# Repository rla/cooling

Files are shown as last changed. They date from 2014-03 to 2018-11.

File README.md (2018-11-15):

# avrcooling

PC cooling controller for rotary cooling devices (fans/pumps). It has
the following features:

 * Supports 4 cooling devices.
 * Can disable devices that still run on minimal PWM.
 * Monitors devices RPM.
 * RPM measurement supports pulse stretching.
 * Supports 2 thermal sensors.
 * Error signal output.
 * Can be controlled/queried over RS-232 interface.
 * Command-line client to query/debug/control the device.
 * Hardware design and source code is MIT-licensed.

### Control algorithm

The control algorithm uses 2 [decision tables](http://en.wikipedia.org/wiki/Decision_table),
one per thermal sensor. Table rows contain the following information:

 * enabled - whether the control row is enable.
 * min_temp - lower bound for activating the control row.
 * max_temp - upper bound for activating the control row.
 * affect_fan0 - whether to apply the row to fan 0.
 * affect_fan1 - whether to apply the row to fan 1.
 * affect_fan2 - whether to apply the row to fan 2.
 * affect_fan3 - whether to apply the row to fan 3.
 * fan0_pwm - PWM value to apply for fan 0.
 * fan1_pwm - PWM value to apply for fan 1.
 * fan2_pwm - PWM value to apply for fan 2.
 * fan3_pwm - PWM value to apply for fan 3.

There are 5 rows in each table. The first row with
min_temp...max_temp range including the current temperature is used for
applying the control values.

All cooling fans start initially in disabled state and with
0 PWM. When a fan PWM is set to a value greater than 0 then the fan power is
enabled. When PWM is set to 0 then the fan is also powered down.

Control table rows are checked periodically. The rows can be
read and updated using the command-line PC app described below.

## Project structure

The project is divided into 3 subdirectories:

 * `avr` - source for microcontroller binary.
 * `hw` - physical hardware design.
 * `pc` - NodeJS command-line app for communication.

## Hardware

### Pin allocation

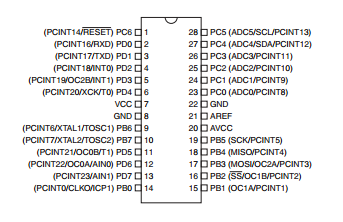
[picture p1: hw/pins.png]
Atmega88 pinout


 * pin  1: reset, connected to VCC and protected by zener diode
 * pin  2: USART RX line (pullup?)
 * pin  3: USART TX line
 * pin  4: PD2, Error signal output
 * pin  5: PD3, OC2B, fan 4 PWM output
 * pin  6: PD4, not connected
 * pin  7: VCC
 * pin  8: GND
 * pin  9: XTAL 1
 * pin 10: XTAL 2
 * pin 11: PD5, OC0B, fan 2 PWM output
 * pin 12: PD6, OC0A, fan 1 PWM output
 * pin 13: PD7, not connected
 * pin 14: PB0, fan 1 enable
 * pin 15: PB1, fan 2 enable
 * pin 16: PB2, fan 3 enable
 * pin 17: PB3, fan 3 PWM output
 * pin 18: PB4, fan 4 enable
 * pin 19: PB5, not connected
 * pin 20: AVCC, connected to VCC through low-pass filter L1/C13
 * pin 21: AREF, analog reference, decoupled with 100nF cap C10
 * pin 22: GND
 * pin 23: PC0, ADC0, temperature sensor 1 input, low-pass filter R5/C7
 * pin 24: PC1, ADC1, temperature sensor 2 input, low-pass filter R3/C8
 * pin 25: PC2, fan 1 RPM input, pull-up, low-pass filter R10/C9
 * pin 26: PC3, fan 2 RPM input, pull-up, low-pass filter R9/C11
 * pin 27: PC4, fan 3 RPM input, pull-up, low-pass filter R8/C12
 * pin 28: PC5, fan 4 RPM input, pull-up, low-pass filter R7/C14

### Port directions

#### Port B

 * PB0 - output (fan 1 enable)
 * PB1 - output (fan 2 enable)
 * PB2 - output (fan 3 enable)
 * PB3 - output (fan 3 PWM)
 * PB4 - output (fan 4 enable)
 * PB5 - output (not connected)
 * PB6 - output (overriden by xtal)
 * PB7 - output (overriden by xtal)

#### Port C

 * PC0 - input (ADC)
 * PC1 - input (ADC)
 * PC2 - input (fan 1 RPM, pull-up)
 * PC3 - input (fan 2 RPM, pull-up)
 * PC4 - input (fan 3 RPM, pull-up)
 * PC5 - input (fan 4 RPM, pull-up)
 * PC6 - input (default reset config)
 * PC7 - not in circuit/registry

#### Port D

 * PD0 - output (overriden by USART)
 * PD1 - output (overriden by USART)
 * PD2 - output (error)
 * PD3 - output (fan 4 PWM)
 * PD4 - output (not connected)
 * PD5 - output (fan 2 PWM)
 * PD6 - output (fan 1 PWM)
 * PD7 - output (not connected)

### Full schematics

Full schematics in Eagle format can be found in the file `hw/schematics.sch`.

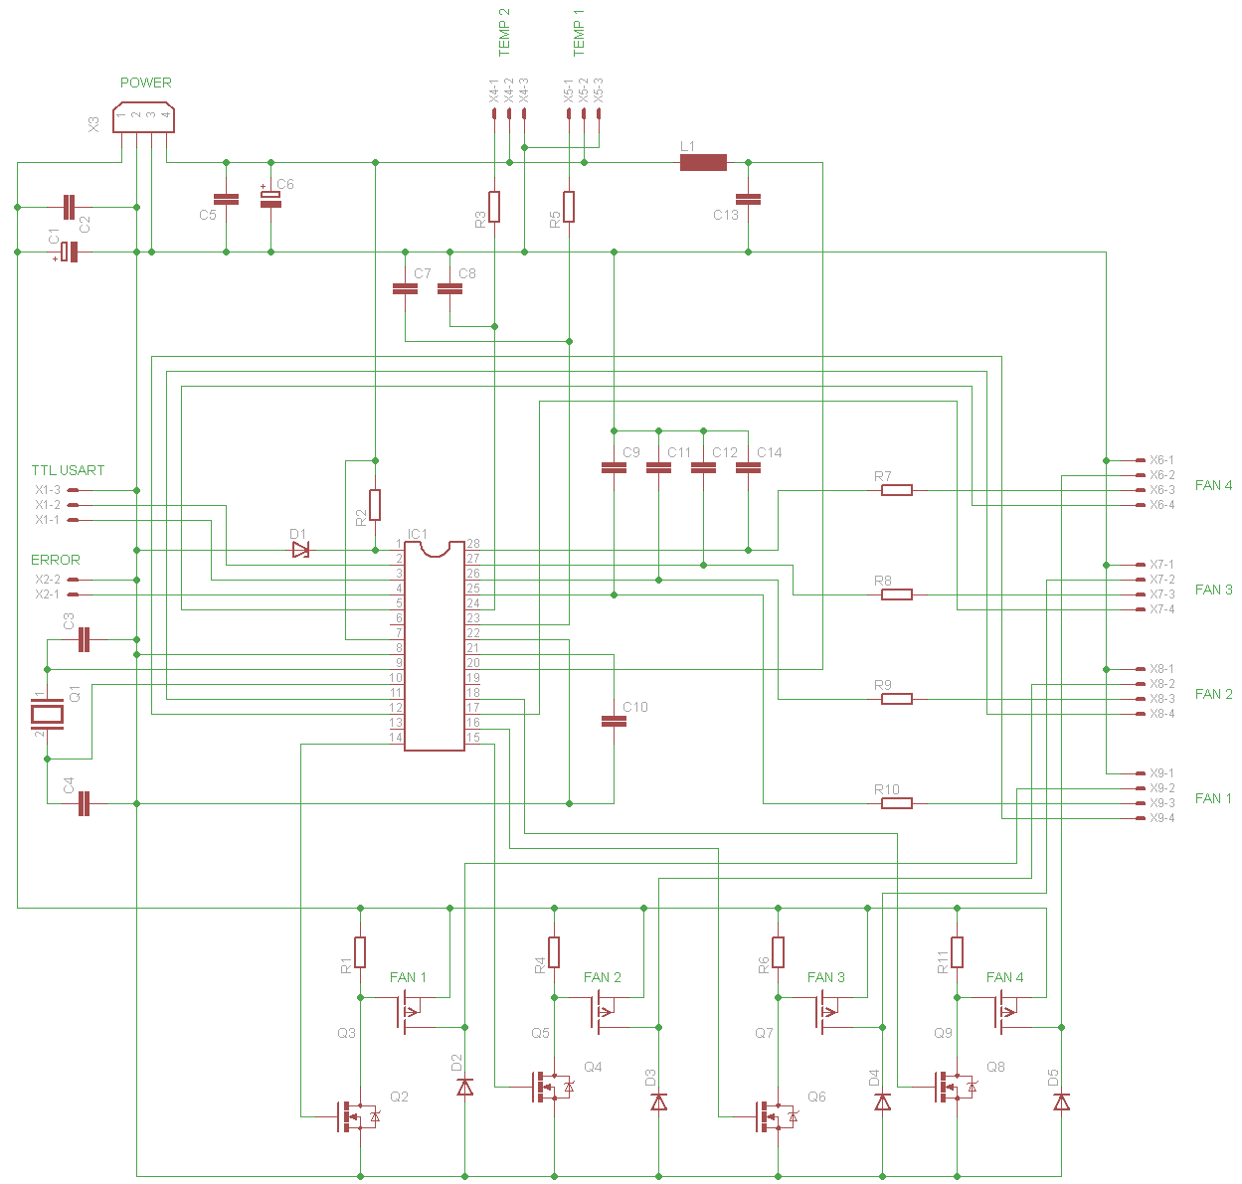
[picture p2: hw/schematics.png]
Full schematics


#### Part list

 * C1 10uF/16V
 * C2 100nF/63V 5mm
 * C3, C4 22pF/63V 2.54mm
 * C5 100nF/63V 5mm
 * C6 10uF/16V 5mm
 * C7, C8 10nF/100V 5mm
 * C9, C11, C12, C14 10nF/63V 5mm
 * C10 100nF/63V 5mm
 * C13 100nF/63V 5mm
 * D1 5.1V zener 7.62mm
 * D2, D3, D4, D5 2N4007
 * IC1 Atmega88 DIP28
 * R1, R2, R3, R4, R5, R6, R7, R8, R9, R10, R11 10k
 * Q1 12MHz
 * Q2, Q4, Q6, Q8 2N7000
 * Q3, Q5, Q7, Q9 IRF9530
 * L1 10uH
 * X3 molex power connector, [Farnell product page](http://uk.farnell.com/jsp/search/productdetail.jsp?SKU=1391827)
 * X6, X7, X8, X9 molex 47053-1000 headers, [Farnell product page](http://uk.farnell.com/jsp/search/productdetail.jsp?SKU=2313705)

### Board layout

Board layout in Eagle format can be found in the file `hw/board.brd`. Layout
suitable for tone-transfer can be found in the PDF file `hw/board.pdf`.

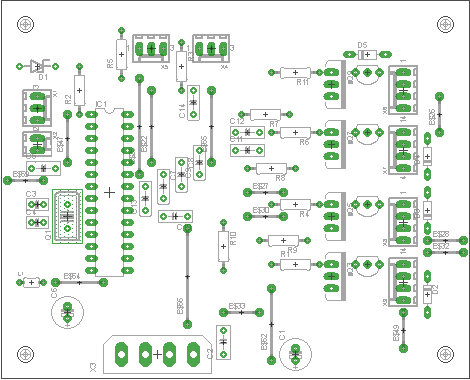
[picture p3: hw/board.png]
Board layout


Photo of 2 completed units:

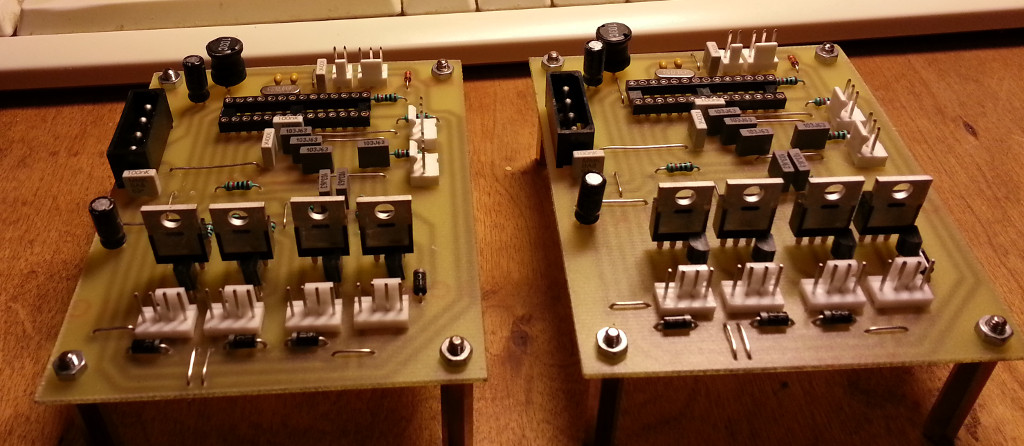
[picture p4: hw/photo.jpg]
2 completed units


### Fan connectors

4-wire connectors are standardized in the [specification](http://www.formfactors.org/developer%5Cspecs%5C4_Wire_PWM_Spec.pdf).
Connector pinout with typical wire colors is:

 * 1 - GND - black
 * 2 - 12V - yellow
 * 3 - RPM - green
 * 4 - PWM - blue

The max fan current is limited by switch MOSFET channel resistance in ON mode.
This is about 0.3 Ohms. Max dissipation of 1W gives the max current of about 1.9A.

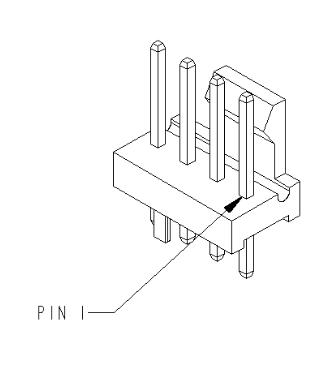
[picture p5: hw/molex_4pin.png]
4-pin molex


#### 3-wire connectors

3-wire connectors lack PWM signal but are otherwise compatible with
4-wire headers. Pinout:

 * 1 - GND - black
 * 2 - 12V - red
 * 3 - RPM - yellow

While a 3-wire fan lacks PWM control, it can still be made variable-speed by
modulating the supply voltage. This can be implemented with the following
circuit:

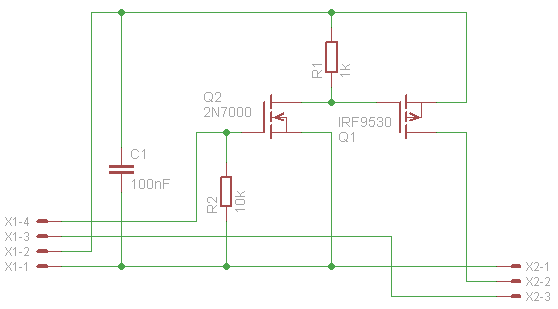
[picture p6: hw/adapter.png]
3-wire to 4-wire adapter


#### Temp. sensor connectors

These connect MCP9700 to the board. There can be up to 2 sensors
connected. The system assumes 0.5V offset and 10mv per °C. This can be
changed by recompiling the firmware.

 * 1 - sensor output
 * 2 - sensor power (5V)
 * 3 - GND

#### Error signal connector

Error signal is set high whenever an enabled fan's RPM
reads 0. The signal comes directly from MCU and cannot
be directly loaded with higher current than 40mA.

 * 1 - error signal
 * 2 - GND

#### RS-232 interface

The RS-232 interface is used for updating the control line tables and
for debugging the device. The connector is denoted as X1 on schematics
and board and has the following pinout:

 * 1 - TX line
 * 2 - RX line
 * 3 - GND

A level translator has to be used for connecting the device to PC. PC
uses signal levels -12V/+12V while the device uses normal TTL levels 0V/5V.

A level translator can be built using the [MAX232](http://www.ti.com/lit/ds/symlink/max232.pdf)
chip or using a prebuilt module/cable/converter. There are various circuits and
building instructions on the Internet.

### Compiling firmware

The project contains a Makefile that includes build targets
with [avr-gcc](http://www.nongnu.org/avr-libc/) compiler.

To build the HEX binary for the controller:

    cd avr
    make

If [avrdude](http://www.nongnu.org/avrdude/) is installed then the hex file
can be burned into the device with the command:

    make burn

### Fuses

 * Clock: Full-swing crystal, BOD enabled
 * BOD 4.3V

#### Low fuse

 * CKDIV8 1 (unprogrammed)
 * CKOUT 1 (unprogrammed)
 * SUT1 0 (crystal, BOD enabled)
 * SUT0 1 (crystal, BOD enabled)
 * CKSEL3 0
 * CKSEL2 1
 * CKSEL1 1
 * CKSEL0 1

CKSEL is for full-swing crystal osc. lfuse total 11010111 = 0xd7.

#### High fuse

 * RSTDISBL 1 (unprogrammed)
 * DWEN 1 (unprogrammed)
 * SPIEN 0 (programmed)
 * WDTON 1 (unprogrammed)
 * EESAVE 1 (unprogrammed)
 * BODLEVEL2 1
 * BODLEVEL1 0
 * BODLEVEL0 0

hfuse total 11011100 = 0xdc.

If avrdude is installed then correct fuses can be burned
using the command:

    make burn-fuse

## Client

The client application is used for updating the control table lines
and for debugging the device.

Client options and supported commands:

```
Usage: avrcooling --port <port> --command <command> [arguments]
Recognized commands:
  disable0       disable fan 0
  disable1       disable fan 1
  disable2       disable fan 2
  disable3       disable fan 3
  echo           sends and receives the given byte
  enable0        enable fan 0
  enable1        enable fan 1
  enable2        enable fan 2
  enable3        enable fan 3
  nostretch0     disable pulse stretch for fan 0
  nostretch1     disable pulse stretch for fan 1
  nostretch2     disable pulse stretch for fan 2
  nostretch3     disable pulse stretch for fan 3
  pwm0_get       query fan 0 PWM level (0-255)
  pwm0_set       set fan 0 PWM (0-255)
  pwm1_get       query fan 1 PWM level (0-255)
  pwm1_set       set fan 1 PWM (0-255)
  pwm2_get       query fan 2 PWM level (0-255)
  pwm2_set       set fan 2 PWM (0-255)
  pwm3_get       query fan 3 PWM level (0-255)
  pwm3_set       set fan 3 PWM (0-255)
  rpm0           query fan 0 RPM
  rpm1           query fan 1 RPM
  rpm2           query fan 2 RPM
  rpm3           query fan 3 RPM
  stretch0       enable pulse stretch for fan 0
  stretch1       enable pulse stretch for fan 1
  stretch2       enable pulse stretch for fan 2
  stretch3       enable pulse stretch for fan 3
  stretch_info   query pulse stretch settings
  temp0          query sensor 0 temperature
  temp0_line_get get control table line (0-4) for sensor 0
  temp0_line_set set control table line (0-4) for sensor 0
  temp1          query sensor 1 temperature
  temp1_line_get get control table line (0-4) for sensor 1
  temp1_line_set set control table line (0-4) for sensor 1

```

### Debugging

Set environment variable `DEBUG=*` and run the command.

    DEBUG=* avrcooling ...

### Installation

Assuming that you have [NodeJS](https://nodejs.org/) installed:

    npm install -g avrcooling

### Protocol

The client-device communication protocol terminates messages with line ends.
Data on individual lines is encoded in the hex encoding.

Decoded commands have the following format:

    [command_byte, arguments..., checksum_byte]

Responses have the following format:

    [response_ok, response arguments..., checksum_byte]

or

    [response_fail, checksum_byte]

or

    [command_checksum_fail, checksum_byte]

Multibyte integers are sent in big-endian format. Maximum decoded message length is 10 bytes.
The detailed description of the protocol is found in [pc/lib/commands.js](pc/lib/commands.js).

The checksum computation uses the Pearson hash algorithm:
<http://en.wikipedia.org/wiki/Pearson_hashing>. The constants
table can be found in [avr/src/pearson.c](avr/src/pearson.c).

## Changelog

 * 2018-11-11 Do not reset PWM on disable. Implement missing get-pwm command.
   Reset RPM only on timeout preventing sporadic 0 RPM responses. Update RPM
   atomically preventing potentially corrupted responses due to data race.
 * 2016-01-31 BOD (brown-out detection) enabled.
 * 2015-03-24 Pulse stretching is implemented. Client code is finished.
 * 2014-07-27 Client code is mostly working.
 * 2014-07-17 AVR code is mostly working.
 * 2014-02-01 Physical hardware design is ready.

## Known issues

 * Max ADC input voltage is 1.1V when the internal reference is selected (by default).
 * Temperature sensor MCP9700 needs 100nF decoupling cap at the sensor to ensure
   stable operation.

## License

The MIT License. See the LICENSE file.

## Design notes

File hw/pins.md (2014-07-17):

# Algorithm

## PWM generation

PWM signal is generated by timers.

## RPM measurement

RPM is measured by finding time between two RPM pulses using the 16-bit Timer1.
Pulses are detected using polling on input pins.

# Atmega88 pin allocation

Atmega88 pinout

 * pin  1: reset, connected to VCC and protected by zener diode
 * pin  2: USART RX line (pullup?)
 * pin  3: USART TX line
 * pin  4: PD2, Error signal output
 * pin  5: PD3, OC2B, fan 4 PWM output
 * pin  6: PD4, not connected
 * pin  7: VCC
 * pin  8: GND
 * pin  9: XTAL 1
 * pin 10: XTAL 2
 * pin 11: PD5, OC0B, fan 2 PWM output
 * pin 12: PD6, OC0A, fan 1 PWM output
 * pin 13: PD7, not connected
 * pin 14: PB0, fan 1 enable
 * pin 15: PB1, fan 2 enable
 * pin 16: PB2, fan 3 enable
 * pin 17: PB3, fan 3 PWM output
 * pin 18: PB4, fan 4 enable
 * pin 19: PB5, not connected
 * pin 20: AVCC, connected to VCC through low-pass filter L1/C13
 * pin 21: AREF, analog reference, decoupled with 100nF cap C10
 * pin 22: GND
 * pin 23: PC0, ADC0, temperature sensor 1 input, low-pass filter R5/C7
 * pin 24: PC1, ADC1, temperature sensor 2 input, low-pass filter R3/C8
 * pin 25: PC2, fan 1 RPM input, pull-up, low-pass filter R10/C9
 * pin 26: PC3, fan 2 RPM input, pull-up, low-pass filter R9/C11
 * pin 27: PC4, fan 3 RPM input, pull-up, low-pass filter R8/C12
 * pin 28: PC5, fan 4 RPM input, pull-up, low-pass filter R7/C14

## Port directions

Port B

 * PB0 - output (fan 1 enable)
 * PB1 - output (fan 2 enable)
 * PB2 - output (fan 3 enable)
 * PB3 - output (fan 3 PWM)
 * PB4 - output (fan 4 enable)
 * PB5 - output (not connected)
 * PB6 - output (overriden by xtal)
 * PB7 - output (overriden by xtal)

Port C

 * PC0 - input (ADC)
 * PC1 - input (ADC)
 * PC2 - input (fan 1 RPM, pull-up)
 * PC3 - input (fan 2 RPM, pull-up)
 * PC4 - input (fan 3 RPM, pull-up)
 * PC5 - input (fan 4 RPM, pull-up)
 * PC6 - input (default reset config)
 * PC7 - not in circuit/registry

Port D

 * PD0 - output (overriden by USART)
 * PD1 - output (overriden by USART)
 * PD2 - output (error)
 * PD3 - output (fan 4 PWM)
 * PD4 - output (not connected)
 * PD5 - output (fan 2 PWM)
 * PD6 - output (fan 1 PWM)
 * PD7 - output (not connected)

## Fuses

Clock selection: full swing crystal

 * CKSEL 0111
 * SUT 11 (slow raising power)
 * Low fuse result: 0xf7

## Registers

 * OSCCAL - Oscillator calibration register - NO CHANGE
 * CLKPR - Clock prescale register - NO CHANGE
 * SMCR - Sleep mode control register - NO CHANGE
 * PRR - Power reduction register - NO CHANGE
 * MCUSR - MCU status register - NO CHANGE
 * WDTCSR - Watchdog timer control register - NO CHANGE
 * MCUCR - MCU control register - interrupts through `sei()`
 * EICRA - External interrupt control register A - NO CHANGE
 * EIMSK - External interrupt mask register - NO CHANGE
 * EIFR - External interrupt flag register - NO CHANGE
 * PCICR - Pin change interrupt control register - NO CHANGE
 * PCIFR - Pin change interrupt flag register - NO CHANGE
 * PCMSK2 - Pin change mask register 2 - NO CHANGE
 * PCMSK1 - Pin change mask register 1 - NO CHANGE
 * PCMSK0 - Pin change mask register 0 - NO CHANGE
 * PINB - The port B input pins address - NOT USED
 * PIND - The port D input pins address - NOT USED
 * GTCCR - General timer/counter control register - NO CHANGE
 * SPCR – SPI control register - NO CHANGE
 * SPSR – SPI status register - NOT USED
 * SPDR – SPI data register - NOT USED

### Port B

 * DDRB - The port B data direction register. As port B is
   configured as output then all bit are set to 1.
 * PORTB - The port B data register. Used for controlling the fans.

### Port C

 * DDRC - The port C data direction register- As port C is used as
   input then no change is needed as it is configured as input by default.
 * PORTC - The port C data register. Some bits need to be written 1 to
   enable pull-ups.
 * PINC - The port C input pins address. Used for polling fans PWM.

### Port D

 * PORTD - The port D data register. Used for error signal. Other
   functions are overriden (USART, PWM).
 * DDRD - The port D data direction register. As port B is configured
   as output then all bit are set to 1.

### Timer 0

Timer 0 needs to be configured in phase-correct PWM mode.

 * TCCR0A - Timer/counter control register A.
 * TCCR0B - Timer/counter control register B.
 * TCNT0 - Timer/counter register.
 * OCR0A - Output compare register A.
 * OCR0B - Output compare register B.
 * TIMSK0 - Timer/counter interrupt mask register - NO CHANGE
 * TIFR0 - Timer/Counter0 interrupt flag register - NO CHANGE

### Timer 1

Timer 1 is used for counting time between RPM pulses and
detecting timeout.

 * TCCR1A – Timer/Counter1 control register A.
 * TCCR1B – Timer/Counter1 control register B.
 * TCCR1C – Timer/Counter1 control register C - NO CHANGE
 * TCNT1H and TCNT1L – Timer/Counter1.
 * OCR1AH and OCR1AL – Output compare register 1 A.
 * OCR1BH and OCR1BL – Output compare register 1 B.
 * ICR1H and ICR1L – Input capture register 1. NO CHANGE/NOT USED
 * TIMSK1 – Timer/Counter1 interrupt mask register
 * TIFR1 – Timer/Counter1 interrupt flag register

### Timer 2

Timer 2 needs to be configured in phase-correct PWM mode.

 * TCCR2A – Timer/counter control register A.
 * TCCR2B – Timer/counter control register B.
 * TCNT2 – Timer/counter register.
 * OCR2A – Output compare register A.
 * OCR2B – Output compare register B.
 * TIMSK2 – Timer/Counter2 interrupt mask register - NO CHANGE
 * TIFR2 – Timer/Counter2 interrupt flag register - NO CHANGE
 * ASSR – Asynchronous status register - NO CHANGE

### USART

TODO

### ADC

ADC reference is set to AVcc.

 * ADCSRB – ADC Control and Status Register B - NO CHANGE
 * ACSR – Analog Comparator Control and Status Register - NO CHANGE
 * DIDR1 – Digital Input Disable Register 1 - NO CHANGE
 * ADMUX – ADC Multiplexer Selection Register
 * ADCSRA – ADC Control and Status Register A
 * ADCL and ADCH – The ADC Data Register
 * ADCSRB – ADC Control and Status Register B
 * DIDR0 – Digital Input Disable Register 0

FIXME - use watchdog?
http://www.embedds.com/using-watchdog-timer-in-your-projects/

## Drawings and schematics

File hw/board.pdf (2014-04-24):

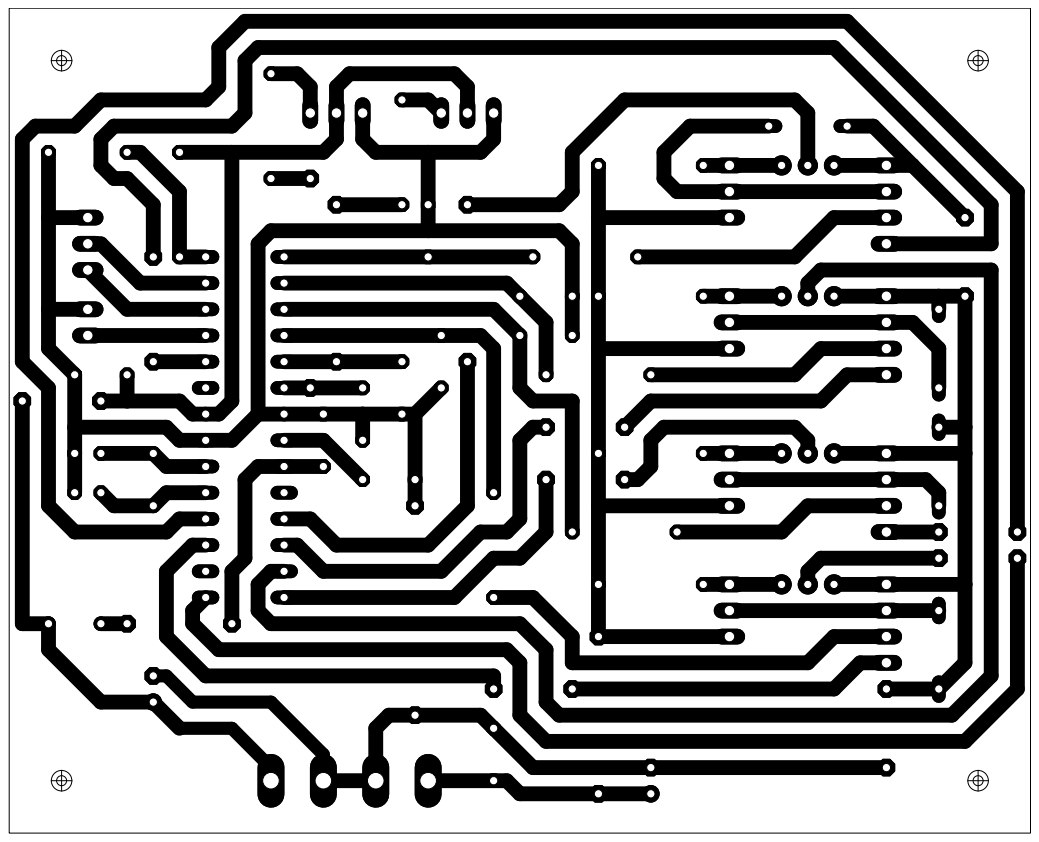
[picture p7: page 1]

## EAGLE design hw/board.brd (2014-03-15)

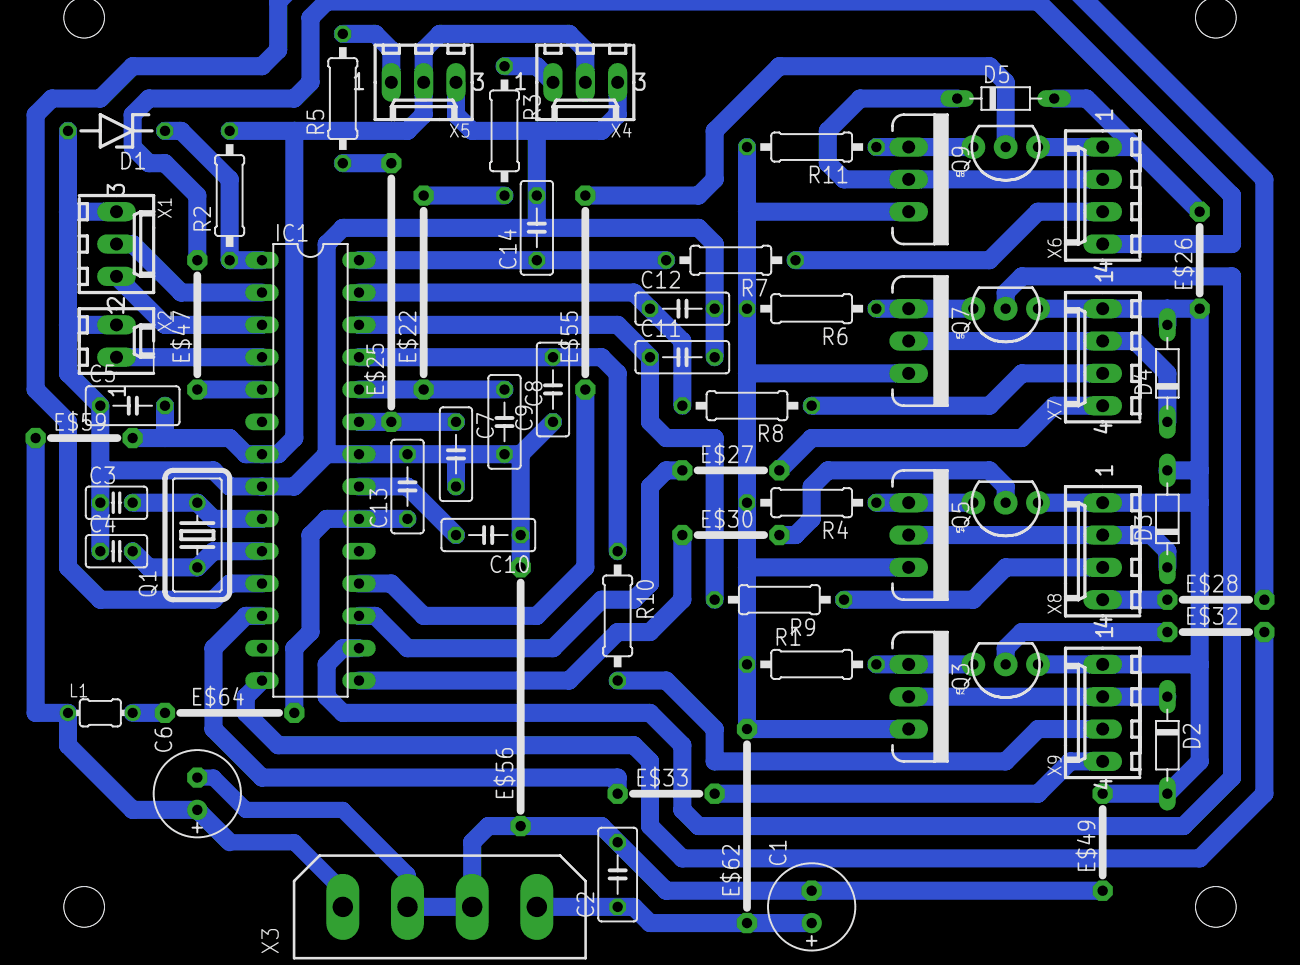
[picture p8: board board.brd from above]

Board: 2 copper layers, 65 parts (0 on the bottom side), 35 nets.

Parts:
C1, C6: E2,5-7
C2, C5: C050-030X075
C3, C4: C025-025X050
C7, C8, C9, C10, C11, C12, C13, C14: C050-025X075
D1: ZDIO-7.5
D2, D3, D4, D5: D-7.5
E$22, E$55, E$62: 15
E$25, E$56: 20
E$26, E$27, E$28, E$30, E$32, E$33, E$49, E$59: 07
E$47, E$64: 10
IC1: DIL28-3
L1: LAL02
Q1: HC18U-V
Q2, Q4, Q6, Q8: TO-92-AMMO
Q3, Q5, Q7, Q9: TO220V
R1, R2, R3, R4, R5, R6, R7, R8, R9, R10, R11: 0207/10
X1, X4, X5: 6410-03
X2: 6410-02
X3: 9090-4V
X6, X7, X8, X9: 6410-04

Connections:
S$1: D2.A, D3.A, D4.A, E$49.2, Q2.1, Q4.1, Q6.1, X7.1, X8.1, X9.1
S$2: D5.C, Q9.2, X6.2
S$3: D4.C, Q7.2, X7.2
S$4: D3.C, Q5.2, X8.2
S$5: D2.C, Q3.2, X9.2
S$6: E$62.2, Q3.3, Q5.3, Q7.3, Q9.3, R1.1, R4.2, R6.2, R11.2
S$8: Q2.3, Q3.1, R1.2
S$9: C11.1, R9.2
S$10: Q6.3, Q7.1, R6.1
S$11: Q8.3, Q9.1, R11.1
S$12: R7.1, X6.3
S$13: R8.1, X7.3
S$14: R9.1, X8.3
S$15: R10.2, X9.3
S$16: C12.1, R8.2
S$17: E$32.1, Q2.2
S$18: C9.2, R10.1
S$20: C5.2, E$59.2, R2.2, X4.2, X5.2
S$22: E$47.2, X6.4
S$24: E$55.2, Q8.2
S$30: E$28.1, X8.4
S$31: C3.1, C4.1, C7.2, C8.2, C9.1, C10.1, C11.2, C12.2, D1.A, E$56.2, X1.3, X2.2, X4.3, X5.3
S$33: D5.A, Q8.1, X6.1
S$34: C13.1, E$64.2
S$38: C3.2, Q1.2
S$39: D1.C, R2.1
S$40: C4.2, Q1.1
S$41: E$22.2, R3.2
S$42: C1.+, E$62.1, X3.4
S$43: R5.2, X5.1
S$45: E$59.1, L1.1, X3.1
S$46: Q4.3, Q5.1, R4.1
S$48: R3.1, X4.1
S$51: C6.-, E$49.1, E$56.1, X3.2, X3.3
S$57: E$64.1, L1.2

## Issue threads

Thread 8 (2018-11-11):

Missing ground in schematic

n3vu0r, 2018-11-11:
In contrast to the board files, the schematic is missing a connection to ground at the wire on the very bottom.

rla, 2018-11-11:
Thank you for pointing it out. I'm going to fix it and re-generate schematics png file too.

rla, 2018-11-19:
Fixed in https://github.com/rla/cooling/commit/cf06339031158de418d635c599184153563e54af

Closed 2018-11-19.

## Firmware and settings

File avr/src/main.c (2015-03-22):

#define F_CPU 12000000UL

#include <avr/io.h>
#include <avr/interrupt.h>
#include <util/delay.h>
#include <util/atomic.h>
#include <avr/eeprom.h>

#include "init.c"
#include "fans.c"
#include "init_fans.c"
#include "adc.c"
#include "measure.c"
#include "rpm.c"
#include "adjust.c"
#include "error.c"
#include "hex.c"
#include "usart_buffer.c"
#include "pearson.c"
#include "protocol.c"
#include "usart_run.c"

int main() {

    init();
    init_fans(0);

    uint8_t start_wait = 0;

    while (1) {

        if (!measure_timeout) {

            rpm_measure();

            if (!measure_timeout) {

                measure_timeout = 1;
            }

            // Wait some time before enabling
            // the adjustment algorithm.

            if (start_wait < 10) {

                start_wait += 1;

            } else {

                adjust();

                check_error();
            }
        }
    };

    return 1;
}

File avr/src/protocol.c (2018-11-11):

#define COMMAND_ADC_0 1
#define COMMAND_ADC_1 2

#define COMMAND_GET_RPM_0 3
#define COMMAND_GET_RPM_1 4
#define COMMAND_GET_RPM_2 5
#define COMMAND_GET_RPM_3 6

#define COMMAND_SET_PWM_0 7
#define COMMAND_SET_PWM_1 8
#define COMMAND_SET_PWM_2 9
#define COMMAND_SET_PWM_3 10

#define COMMAND_GET_PWM_0 11
#define COMMAND_GET_PWM_1 12
#define COMMAND_GET_PWM_2 13
#define COMMAND_GET_PWM_3 14

#define COMMAND_ENABLE_0 15
#define COMMAND_ENABLE_1 16
#define COMMAND_ENABLE_2 17
#define COMMAND_ENABLE_3 18

#define COMMAND_DISABLE_0 19
#define COMMAND_DISABLE_1 20
#define COMMAND_DISABLE_2 21
#define COMMAND_DISABLE_3 22

#define COMMAND_TEMP0_SET 23
#define COMMAND_TEMP1_SET 24

#define COMMAND_TEMP0_GET 25
#define COMMAND_TEMP1_GET 26

#define COMMAND_GET_STRETCH 27

#define COMMAND_STRETCH_ENABLE_0 28
#define COMMAND_STRETCH_ENABLE_1 29
#define COMMAND_STRETCH_ENABLE_2 30
#define COMMAND_STRETCH_ENABLE_3 31

#define COMMAND_STRETCH_DISABLE_0 32
#define COMMAND_STRETCH_DISABLE_1 33
#define COMMAND_STRETCH_DISABLE_2 34
#define COMMAND_STRETCH_DISABLE_3 35

#define COMMAND_ECHO 254

#define RESPONSE_OK 255
#define RESPONSE_FAIL 254
#define RESPONSE_CHECKSUM_FAIL 253

// Must be <= USART_BUFFER_SIZE

#define PROTOCOL_BUFFER_SIZE 20

volatile uint8_t protocol_recv_buffer[PROTOCOL_BUFFER_SIZE];
volatile uint8_t protocol_recv_buffer_length = 0;

volatile uint8_t protocol_send_buffer[PROTOCOL_BUFFER_SIZE];
volatile uint8_t protocol_send_buffer_length = 0;

// Resets the send buffer.

void protocol_send_buffer_reset() {

    protocol_send_buffer_length = 0;
}

// Puts byte into send buffer.

void protocol_send_buffer_put(uint8_t byte) {

    if (protocol_send_buffer_length < PROTOCOL_BUFFER_SIZE) {

        protocol_send_buffer[protocol_send_buffer_length] = byte;
        protocol_send_buffer_length += 1;
    }
}

// Adds Pearson hash value into sending buffer.

void protocol_send_buffer_put_crc() {

    protocol_send_buffer_put(pearson_hash(
        protocol_send_buffer, 0, protocol_send_buffer_length));
}

// Verifies the checksum of currently
// received data.

uint8_t protocol_verify() {

    // Checksum is the last received byte.

    uint8_t check = protocol_recv_buffer[protocol_recv_buffer_length - 1];

    return check == pearson_hash(
        protocol_recv_buffer, 0, protocol_recv_buffer_length - 1);
}

// Reads the control line from
// the receive buffer.
// This must be consistent with the
// t_temp_line definition.

void protocol_read_control_line(t_temp_line *line) {

    line->control = protocol_recv_buffer[2];
    line->min_temp = protocol_recv_buffer[3];
    line->max_temp = protocol_recv_buffer[4];
    line->fan0_pwm = protocol_recv_buffer[5];
    line->fan1_pwm = protocol_recv_buffer[6];
    line->fan2_pwm = protocol_recv_buffer[7];
    line->fan3_pwm = protocol_recv_buffer[8];
}

// Puts the control line data into
// the send buffer.

void protocol_put_control_line(t_temp_line *line) {

    protocol_send_buffer_put(line->control);
    protocol_send_buffer_put(line->min_temp);
    protocol_send_buffer_put(line->max_temp);
    protocol_send_buffer_put(line->fan0_pwm);
    protocol_send_buffer_put(line->fan1_pwm);
    protocol_send_buffer_put(line->fan2_pwm);
    protocol_send_buffer_put(line->fan3_pwm);
}

// Sets a control line for temperature 0.

uint8_t protocol_command_run_set_temp0() {

    t_temp_line line;

    // Line index.

    uint8_t i = protocol_recv_buffer[1];

    if (i >= 5) {

        return 0;
    }

    protocol_read_control_line(&line);

    adjust_write_temp0_line(i, &line);

    return 1;
}

// Sets a control line for temperature 1.

uint8_t protocol_command_run_set_temp1() {

    t_temp_line line;

    // Line index.

    uint8_t i = protocol_recv_buffer[1];

    if (i >= 5) {

        return 0;
    }

    protocol_read_control_line(&line);

    adjust_write_temp1_line(i, &line);

    return 1;
}

// Reads and saves a sensor 0 control line.

void protocol_command_run_get_temp0() {

    t_temp_line line;

    uint8_t i = protocol_recv_buffer[1];

    if (i >= 5) {

        protocol_send_buffer_put(RESPONSE_FAIL);

        return;
    }

    adjust_read_temp0_line(i, &line);

    protocol_send_buffer_put(RESPONSE_OK);

    protocol_put_control_line(&line);
}

// Reads and saves a sensor 0 control line.

void protocol_command_run_get_temp1() {

    t_temp_line line;

    uint8_t i = protocol_recv_buffer[1];

    if (i >= 5) {

        protocol_send_buffer_put(RESPONSE_FAIL);

        return;
    }

    adjust_read_temp1_line(i, &line);

    protocol_send_buffer_put(RESPONSE_OK);

    protocol_put_control_line(&line);
}

// Runs the decoded command.

void protocol_command_run() {

    uint8_t command = protocol_recv_buffer[0];

    switch (command) {

        case COMMAND_ADC_0:

            protocol_send_buffer_put(RESPONSE_OK);
            protocol_send_buffer_put(temperature_0);

        break;

        case COMMAND_ADC_1:

            protocol_send_buffer_put(RESPONSE_OK);
            protocol_send_buffer_put(temperature_1);

        break;

        case COMMAND_GET_RPM_0:

            protocol_send_buffer_put(RESPONSE_OK);
            protocol_send_buffer_put((uint8_t) (rpm_0 >> 8));
            protocol_send_buffer_put((uint8_t) rpm_0);

        break;

        case COMMAND_GET_RPM_1:

            protocol_send_buffer_put(RESPONSE_OK);
            protocol_send_buffer_put((uint8_t) (rpm_1 >> 8));
            protocol_send_buffer_put((uint8_t) rpm_1);

        break;

        case COMMAND_GET_RPM_2:

            protocol_send_buffer_put(RESPONSE_OK);
            protocol_send_buffer_put((uint8_t) (rpm_2 >> 8));
            protocol_send_buffer_put((uint8_t) rpm_2);

        break;

        case COMMAND_GET_RPM_3:

            protocol_send_buffer_put(RESPONSE_OK);
            protocol_send_buffer_put((uint8_t) (rpm_3 >> 8));
            protocol_send_buffer_put((uint8_t) rpm_3);

        break;

        case COMMAND_SET_PWM_0:

            fan_set_pwm(0, protocol_recv_buffer[1]);
            protocol_send_buffer_put(RESPONSE_OK);

        break;

        case COMMAND_SET_PWM_1:

            fan_set_pwm(1, protocol_recv_buffer[1]);
            protocol_send_buffer_put(RESPONSE_OK);

        break;

        case COMMAND_SET_PWM_2:

            fan_set_pwm(2, protocol_recv_buffer[1]);
            protocol_send_buffer_put(RESPONSE_OK);

        break;

        case COMMAND_SET_PWM_3:

            fan_set_pwm(3, protocol_recv_buffer[1]);
            protocol_send_buffer_put(RESPONSE_OK);

        break;

        case COMMAND_GET_PWM_0:

            protocol_send_buffer_put(RESPONSE_OK);
            protocol_send_buffer_put(fan_get_pwm(0));

        break;

        case COMMAND_GET_PWM_1:

            protocol_send_buffer_put(RESPONSE_OK);
            protocol_send_buffer_put(fan_get_pwm(1));

        break;

        case COMMAND_GET_PWM_2:
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

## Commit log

2014-07-27 Init timer 2 for fan 2 and 3 PWM
2014-07-30 Primitive adjustment algorithm, error setting, fan init
    [adjust.c, main.c]
2014-08-01 Fan connector description
2015-03-23 Init fans with 0 PWM
2015-03-23 0-based indexing for sensor/fan naming
2015-03-25 Add 3-wire to 4-wire adapter
2015-04-02 Describe error output and temp. sensor inputs
2016-01-31 New fuses+documentation
2018-11-11 Reset RPM only on timeout.
    This prevents sporadic 0 RPM responses.
2018-11-11 Implement missing get-pwm command.
    [protocol.c]
2018-11-11 Do not reset PWM on disable.
    Removes surprising and undocumented behavior.
    [protocol.c]
2018-11-19 Add missing ground connection to output MOSFET switches
    [schematics.sch]
2018-11-19 Regenerate schematics PNG file

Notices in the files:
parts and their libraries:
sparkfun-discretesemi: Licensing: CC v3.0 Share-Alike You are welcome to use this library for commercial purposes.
